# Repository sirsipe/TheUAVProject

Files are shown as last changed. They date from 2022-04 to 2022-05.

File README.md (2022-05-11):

# The UAV Project

Motivation of this project is absolutely nothing else than learning & for fun. Some years ago I bought a cheap amateur RC plane just to try the hobby and soon realized that I have drawers full of Arduinos, Raspberry Pies and other nerdy stuff I'd love to fly to the moon. So here we go!

**!!! WORK IN PROGRESS !!!**

**Agenda:** _~1,5m wingspan hobby-grade RC plane with on-board Raspberry Pi flight computer running custom firmware._

## Brief 

**Arduino Pro Mini** reads PWM signals of the on-board **RC receiver** and re-routes the signals to **PWM Driver** (PCA9685) as I2C master device. The PWM Driver controls the engine and all servos.

RPi sends its display using the analog TV out with **FPV transmitter** (TX5258). The display will have **live camera feed** and overlay with available **flight data**. When the RPi boots up and has its **custom firmware** running, it will notify Arduino with a continues ping that Arduino should switch to I2C slave mode, and RPi will become I2C master.
 
When RPi is I2C master, it will first query PWM values from Arduino and then send them to Servo driver. Since RPi can also query **orientation from MPU9250** and **position from GPS**, it is possible to write **autoleveling, autopilot and such routines**.

The radio has 6 channels and 2 of them (knobs) will be utilized to access **flight menu** of the custom OSD software.

## Stuff used

- An RC Plane (6CH): [Hobbyking Bix3 /w Flaps](https://hobbyking.com/en_us/hobbykingtm-bix3-trainer-fpv-epo-1550mm-mode-2-ready-to-fly.html?___store=en_us)
  - Hobbyking radio + 6CH receiver
  - ESC with 5v BEC
- FPV Transmitter: [Eachine TX5258](https://www.banggood.com/Eachine-TX5258-5_8G-72CH-25-or-200-or-500-or-800mW-Switchable-FPV-Transmitter-Support-OSD-Configuring-Smartaudio-p-1248768.html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): _Power from battery's balanced connector_
- FPV Receiver: [Eachine VR D2 Pro](https://www.getfpv.com/eachine-vr-d2-pro-40ch-5-8g-diversity-fpv-goggles-with-dvr.html)
- [Arduino Pro Mini 5v](https://www.adafruit.com/product/2378): _Power from ESC BEC_
- [Raspberry Pi 0w](https://www.raspberrypi.com/products/raspberry-pi-zero-w/) + [Camera](https://thepihut.com/products/zerocam-camera-for-raspberry-pi-zero): _According to [this page](https://raspi.tv/2017/how-much-power-does-pi-zero-w-use), current draw when recording video is around 230mA. In addition Beitian BN-880 GPS draws 50mA@5V, but it will be run at 3v3. Eachine TX5258 can supply 300mA so... not much playroom there :)_
- [Beitian BN-880 GPS](https://uk.banggood.com/Beitian-BN-880-Flight-Control-GPS-Module-Dual-Module-Compass-With-Cable-for-RC-Drone-FPV-Racing-p-971082.html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): _Power from RPi (3v3)_
- GY-91 (MPU9250+BMP280) 10-DOF sensor: _Power from RPi (3v3)_

## Initial schematics

**Note**: Picure is not up-to-date. *GY-91 (MPU9250+BMP280) 10-DOF sensor* is actually connected to 3v3 side of the I2C bus and gets powered by RPi's 3v3 line.
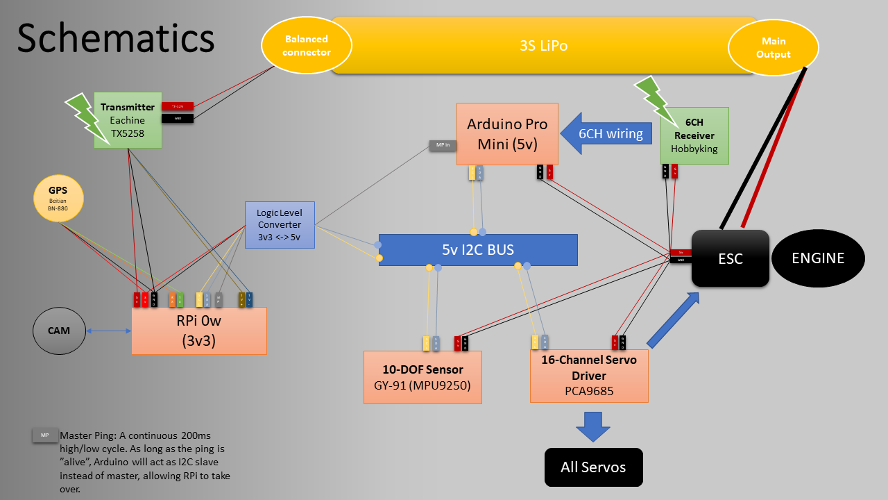
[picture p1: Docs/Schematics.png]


## RPi Zero W install instructions

    git clone https://github.com/sirsipe/TheUAVProject
    cd TheUAVProject
    git submodule init 
    git submodule update
    cd RaspberryPi/buildroot
    make BR2_EXTERNAL=../buildroot-externals rpi0w-uav_defconfig
    make menuconfig
    
Now at buildroot configuration, navigate down to `External options` and choose `cam-on-start`, `osd` and `osd-on-start`. You can also selected `rpi-wifi`, navigate inside it and configure the RPi for headless SSH access. Exit and save.

    make

The resulting image can be found from `output/images/sdcard.img`.

## Progress

- [x] Custom Linux with Buildroot for RPi 0w
  - [x] Raspivid working
  - [x] GPS via UART working
  - [x] [Raylib](https://github.com/raysan5/raylib) working (for custom OSD)
  - [x] OSD software base
    - [ ] PWM from Arduino to servos
      - [ ] Menu navigation using CH5/6
        - [ ] Subsystem control (record/stop, flaps, auto-level, set home, return to home...) 
    - [ ] GPS altitude & speed
    - [ ] GPS flight path 
    - [ ] Pitch, yaw, roll
  - [x] Master Ping -line
  - [x] I2C
    - [ ] GY-91 communication
  - [x] Power from Trasmitter

- [x] 6CH PWM signals from RC receiver for Arduino Pro Mini
  - [x] Re-route received signals to servo driver
  - [x] Power from ESC
  - [x] I2C slave mode

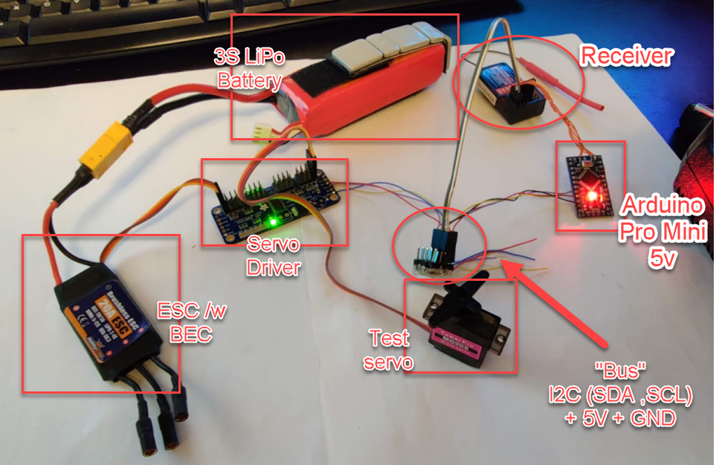
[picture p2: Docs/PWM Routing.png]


## Unrelated picture



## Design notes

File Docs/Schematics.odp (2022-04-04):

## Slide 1

Schematics

Balanced connector

3S LiPo

Main Output

Transmitter Eachine

TX5258

~7-12V

Arduino Pro Mini (5v)

6CH Receiver Hobbyking

GND

MP in

6CH wiring

GPS
Beitian BN-880

SCL

SDA

GND

5v

GND

5v

Logic Level Converter
3v3 <-> 5v

5v I2C BUS

5v

GND

ESC

ENGINE

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
RPi 0w

(3v3)

10-DOF Sensor
GY-91 (MPU9250)

SCL

SDA

5v

GND

16-Channel Servo Driver
PCA9685

SCL

SDA

5v

GND

MP

Master Ping: A continuous 200ms high/low cycle. As long as the ping is ”alive”, Arduino will act as I2C slave instead of master, allowing RPi to take over.

All Servos

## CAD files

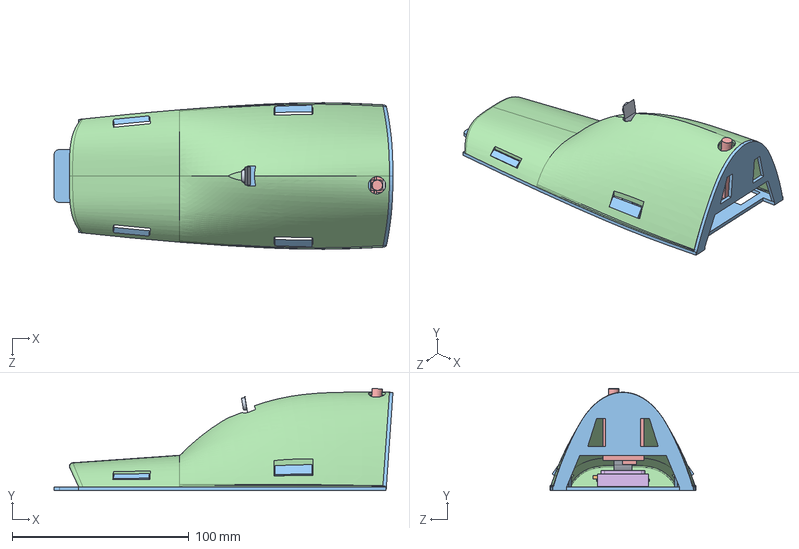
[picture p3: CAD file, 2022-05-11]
DesignAnd3DPrints/SOLIDWORKS/canopy.SLDASM
191.9 x 57.9 x 82.9 mm
RPI Camera
RPi Zero
Bix3_canopy_bottom
Bix3_canopy_top_v4
Transmitter
gps

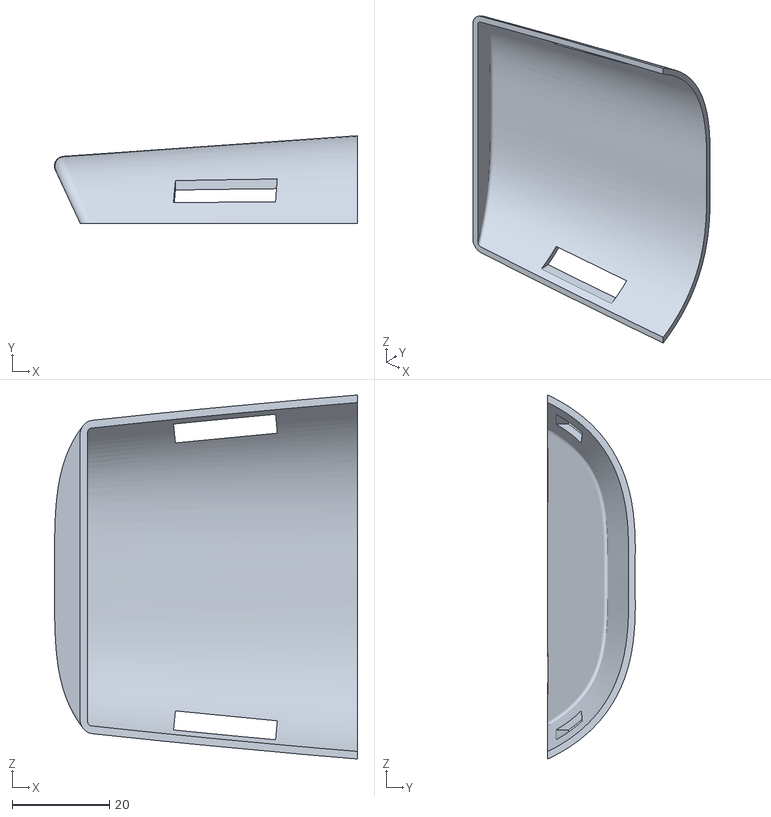
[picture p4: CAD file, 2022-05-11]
DesignAnd3DPrints/canopy_top2.STL
62.4 x 18.0 x 75.0

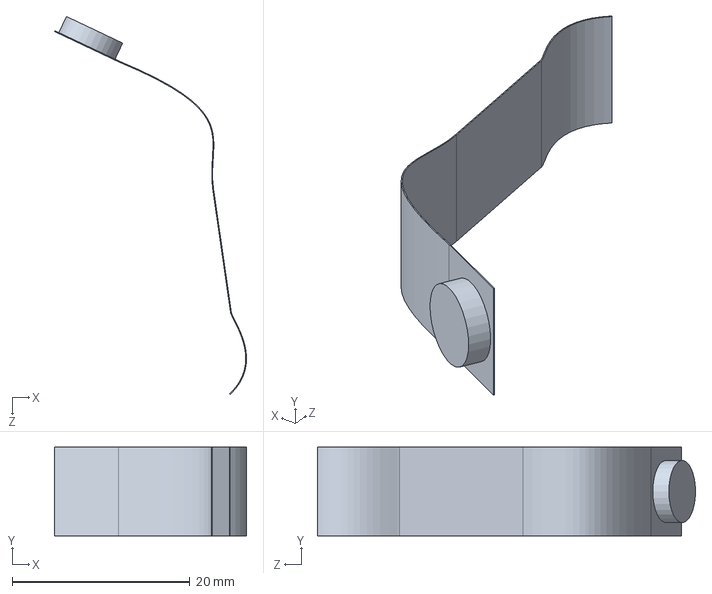
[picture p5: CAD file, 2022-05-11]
DesignAnd3DPrints/SOLIDWORKS/RPI Camera.SLDPRT
21.6 x 10.0 x 42.5 mm

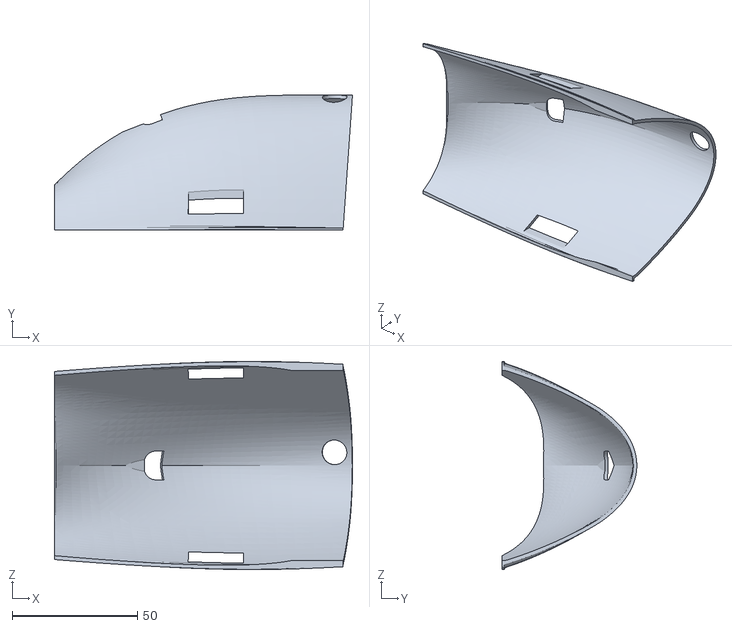
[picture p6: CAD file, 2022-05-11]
DesignAnd3DPrints/canopy_top1.STL
118.8 x 53.8 x 82.9

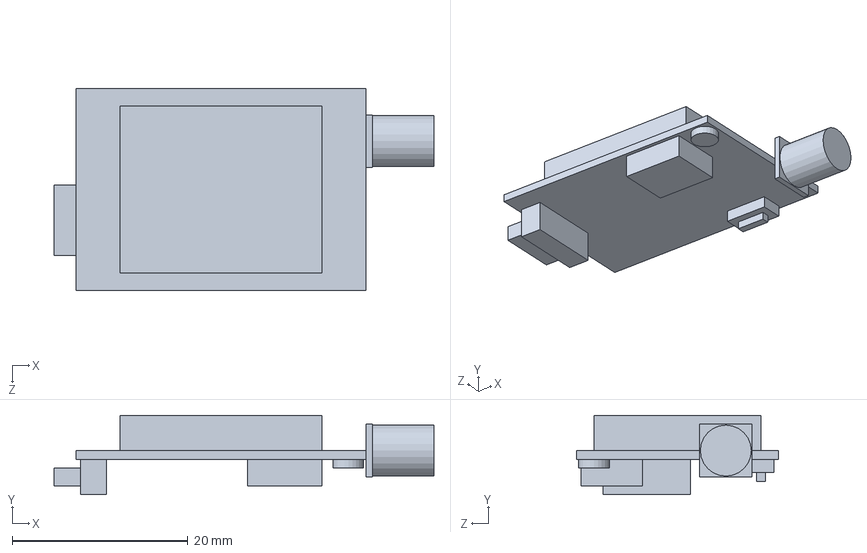
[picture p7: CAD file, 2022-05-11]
DesignAnd3DPrints/SOLIDWORKS/Transmitter.SLDPRT
43.2 x 9.00 x 23.0 mm

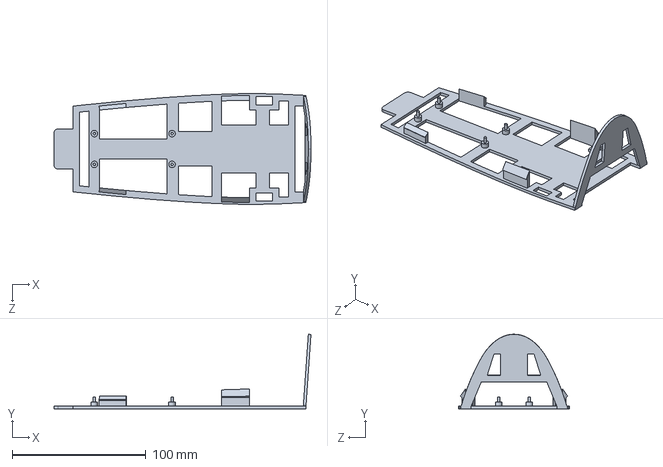
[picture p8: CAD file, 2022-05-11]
DesignAnd3DPrints/SOLIDWORKS/Bix3_canopy_bottom.SLDPRT
191.9 x 55.7 x 82.7 mm

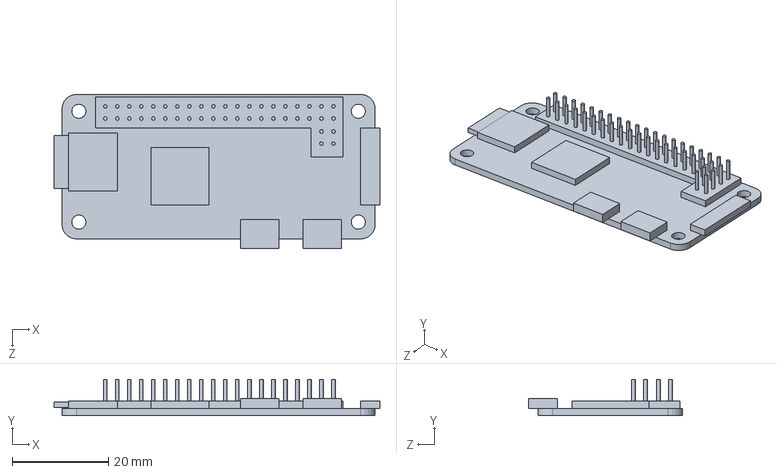
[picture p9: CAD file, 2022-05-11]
DesignAnd3DPrints/SOLIDWORKS/RPi Zero.SLDPRT
67.7 x 7.50 x 32.0 mm

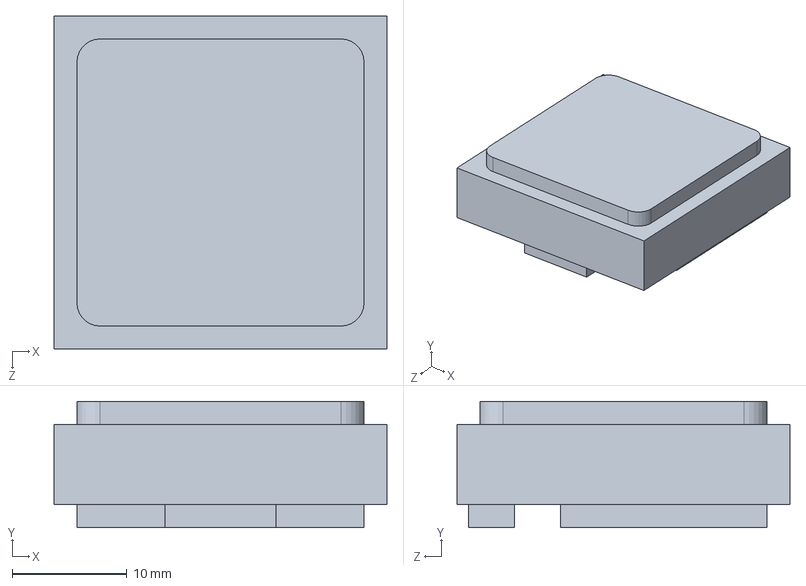
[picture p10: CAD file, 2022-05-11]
DesignAnd3DPrints/SOLIDWORKS/gps.SLDPRT
29.0 x 11.0 x 29.0 mm

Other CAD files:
DesignAnd3DPrints/SOLIDWORKS/Bix3_canopy_top_v4.SLDPRT
DesignAnd3DPrints/Bix3_canopy_bottom.STL

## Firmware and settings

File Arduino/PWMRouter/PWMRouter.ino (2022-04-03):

// NEED Libraries:
// - Adafruit PWM Servo Driver Library
// - EnableInterrupt

#include <EnableInterrupt.h>
#include "Adafruit_PWMServoDriver.h"

#define CHANNELS 6
#define DIGITAL_PINS 3, 5, 6, 9, 10, 11

const byte _InputPins[CHANNELS] = { DIGITAL_PINS };

// Cache
volatile uint16_t _PWMValues[CHANNELS] = { 0 };

Adafruit_PWMServoDriver pwmDriver = Adafruit_PWMServoDriver();
#define PWM_FREQ 50

void GetPWMData(uint16_t channels[CHANNELS])
{
  for(uint16_t ch = 0; ch < CHANNELS; ch++)
    channels[ch] = _PWMValues[ch]; 
}


// Some syntactic sugar to ease up handler declarations. CH_HANDLER_NAME(X) 
// pre-compiles into chX_handler which can be used as function name.
#define CH_HANDLER_NAME(x) ch##x##_handler

#define CHANNEL_HANDLER(x) \
  void CH_HANDLER_NAME(x) () { \
    const uint8_t chIndex = x - 1; \
    const byte UNKNOWN_STATUS = 99; \
    static byte lastStatus = UNKNOWN_STATUS; \
    static uint32_t start = 0; \
    switch (lastStatus) { \
      case UNKNOWN_STATUS: \
      { \
        lastStatus = digitalRead(_InputPins[chIndex]) == HIGH ? LOW : HIGH; \
        break; \
      } \
      case HIGH: \
      { \
        lastStatus = LOW; \
        start = micros(); \
        break; \
      } \
      case LOW: \
      { \
        lastStatus = HIGH; \
        uint16_t value = micros() - start; \
        _PWMValues[chIndex] = value; \
        break; \
      } \
    }\
  }

// Cherry on the top: Setup the handler
#define SETUP_CH_HANDLER(x) \
  pinMode(_InputPins[x-1], INPUT); \
  enableInterrupt(_InputPins[x-1], CH_HANDLER_NAME(x), CHANGE);


void setup() {
  SETUP_CH_HANDLER(1);
  SETUP_CH_HANDLER(2);
  SETUP_CH_HANDLER(3);
  SETUP_CH_HANDLER(4);
  SETUP_CH_HANDLER(5);
  SETUP_CH_HANDLER(6);
  
  pwmDriver.begin();
  pwmDriver.setPWMFreq(PWM_FREQ);
  
}
void loop() {
  uint16_t values[CHANNELS];
  GetPWMData(values);

  for (int i = 0; i < CHANNELS; i++)
  {
    if (values[i])
      setServoPulse(i, values[i]);
  }  
}


CHANNEL_HANDLER(1)
CHANNEL_HANDLER(2)
CHANNEL_HANDLER(3)
CHANNEL_HANDLER(4)
CHANNEL_HANDLER(5)
CHANNEL_HANDLER(6)


void setServoPulse(uint8_t n, double pulse) {

  double pulselength = 1000000;   // 1,000,000 us per second
  pulselength /= PWM_FREQ;   
  pulselength /= 4096;  // 12 bits of resolution
  pulse /= pulselength;
  pwmDriver.setPWM(n, 0, pulse);
    
}

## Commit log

2022-04-03 Arduino PWM Router
2022-04-04 PWM Routing pic
2022-05-11 SOLIDWORKS design of Bix3 canopy and STLs for 3D Printing
    [Bix3_canopy_bottom.SLDPRT, Bix3_canopy_bottom.STL, Bix3_canopy_top_v4.SLDPRT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]
